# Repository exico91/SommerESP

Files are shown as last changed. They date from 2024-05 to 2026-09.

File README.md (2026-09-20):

# 🏠 SommerESP

A plug and play ESP32-C3 board to control Sommer garage doors based on ESPHOME

This combo is designed to replace the Sommer Conex Module and the Sommer Output OC Module. 

## ⚙️ How it works
The Sommer Conex Module is designed to replicate the press of the buttons on the controller of the garage door and the Sommer Output OC just provide the signal for the status and 24 Volts DC.  

This project takes the 24V and converts it to 3.3V for the ESP32-C3 module, the DC regulator on the power board can take from 4.5V to 40V and cleanly output 3.3V then transfer it to the Control board along with the status signal.  

The ESP controller simulate the press of the buttons using a pair of optocouplers, simple enough. You can also attach other things to this board, I left a couple of GPIOs on exposed pins along with the serial connection required to flash the module.

## 📋 Instructions
You can buy [here](https://www.tindie.com/products/exico91/sommeresp/) the kit that includes the two boards and a cable or you can build one yourself. You can find the BOM (bill of materials) [here](https://htmlpreview.github.io/?https://github.com/exico91/SommerESP/blob/main/Kicad/SommerESP/bom/ibom.html) and the gerber files [here](/Kicad/SommerESP/gerbers/). 
There are a lot of PCB Manufacturers. The most known are [PCBWay](https://www.pcbway.com/) and [JLCPCB](https://jlcpcb.com/). I used both and are good.

### 🔧 Installation
 1. Remove the plug from the wall, or cut off power to the Sommer garage door controller
 2. Write your firmware if you want or use it as is. You can find a basic yaml [here](/ESPHOME/esphome.yaml) or the ethernet module variant [here](/ESPHOME/esphome-eth.yaml). To do so you will need a serial programmer and set it to 3.3V, connect GND, VIN, RX and TX to the controller board and power it on while pressing BOOT on the board. When you are done remove the serial programmer. DO NOT connect the programmer while the board is connected to the power board or inserted in the Sommer controller.
 3. Open the controller but pay attention to the keypad cable when you remove the cover
 4. Place the board as shown, pay attention that both plugs are inserted:
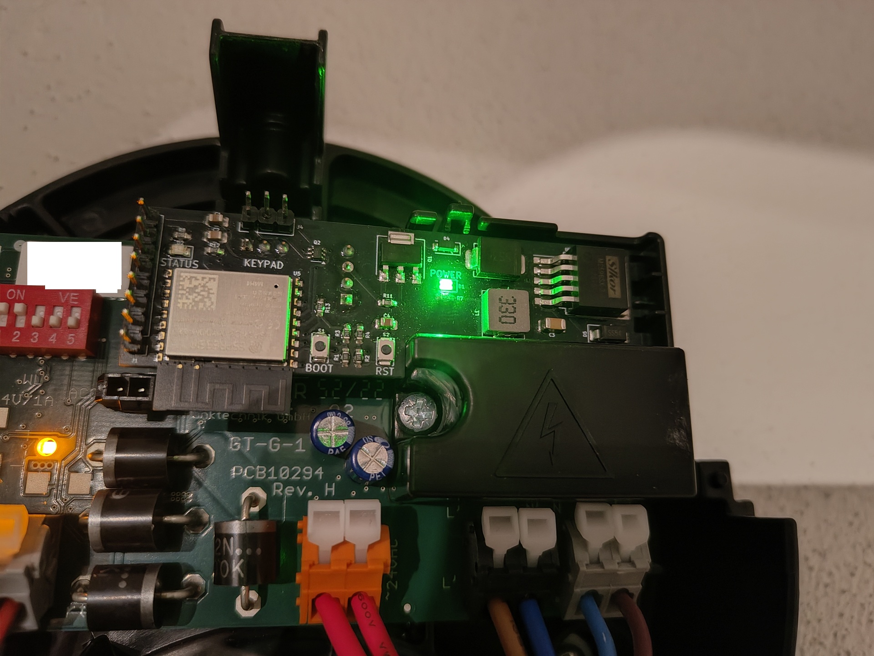
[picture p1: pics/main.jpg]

 5. Flip the first two switches to ON on the dip switch array on the Sommer controller
 6. Connect the keypad to the board in the same orientation as it was before (if present, some Sommers do not have a keypad)
 7. Close the cover and power it on. You should be able to see a wifi network and connect to it to configure the module.

> [!NOTE]
> The ethernet module (W5500) yaml is available [here](/ESPHOME/esphome-eth.yaml) and the KiCad project [here](/Kicad/SommerESP-ETHmodule/).

### 📡 External Antenna

If your installation requires better WiFi reception, an external antenna version is available. You will need:
 1. The SommerESP board in the version **without integrated antenna**, available on the [Tindie store](https://www.tindie.com/stores/exico91/)
 2. The **antenna kit** (includes antenna and U.FL adapter cable), also available on the [Tindie store](https://www.tindie.com/stores/exico91/)

Connect the adapter cable to the U.FL connector on the board and attach the external antenna.

### 🔌 Flashing and extra pins
To flash connect you serial programmer to the exposed pins on the controller board. DO NOT connect the programmer while the board is connected to the power board or inserted in the Sommer controller.
From top to bottom the pins are in this order:

3.3V
GPIO05
RX
TX
GPIO18
GPIO19
GPIO03
GND

Press BOOT while powering on the programmer to send the controller in flashing mode.

### 🔄 Factory reset
With the provided yaml, holding the BOOT button for 10 seconds and then releasing it factory resets the board (erases the saved Wi-Fi credentials and preferences, then reboots). It can also be triggered from Home Assistant with the "Factory Reset" button.

## ✅ Compatibility
This project should work with Sommer Base+, Pro+ and Evo+.
The main focus of this project is ESPHome and Homeassistant but you can flash whatever you want on the ESP32-C3.
Check [here](/pinout.md) for the pinout.

**Confirmed working models:**

| **Model**  | **Notes** | **Credits** |
|---|---|---|
| 9080 Base+ | The keypad plug is present but there is no keypad, just plug the SommerESP there. | tim-kiefer  |
| 2060 Evo+  | The keypad plug has 5 pins instead of 3. Just plug the module on the middle leaving pin 1 and 5 free. See photo for reference [here](/pics/2060+notes.jpg) | Severnt |
| 9110 Pro+  | Original installation that created this project. This model has a wall mount control board with a 2 button keypad. | Alessio D |
| S 9050 pro | Need to manually add the DIP switch selector. Check [here](https://github.com/exico91/SommerESP/issues/5#issuecomment-2755661908) | M3c4tr0x |
| A800 XL    | Compatible but the Conex pins are shifted. Requires board version 2 or jumper cables.                                                                    | [jkremlacek](https://github.com/jkremlacek) |

> [!WARNING]
> Please do check the distance between the power pins and the right pin on the button connector. This version of SommerESP is compatible with Sommer boards where the distance is around 9.5 mm or 7.5 mm, just check which is correct and solder the connector for the Conex section in the 9.5 (default) or 7.5 place. If you are buying from Tindie the default will be 9.5, if you need 7.5 please contact me.

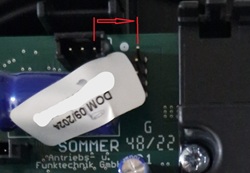
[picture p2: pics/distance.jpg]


## 📦 Release Log

### Firmware Release Log

| **Version** | **ESPHome** | **Changes** |
|---|---|---|
| 1.0 | — | Initial release |
| 1.3 | 2024.6.1 | Added compatibility for ESPHome 2024.6.1 |
| 2.0 | 2025.8.3 | Added compatibility for ESPHome 2025.8.3 |
| 3.0 | 2026.5.3 | Added compatibility for ESPHome 2026.5.3+, added Ethernet module version |
| 3.1 | 2026.5.3 | Cover stop function is now working |
| 3.2 | 2026.9.0 | Added factory reset function to the BOOT button (hold for 10 seconds) |

### Hardware Release Log

| **Version** | **Changes** |
|---|---|
| 1.0 - 2.0 | Dual board module with cable |
| 3.0 | Single board, adds Ethernet compatibility. Supports only 9.5 mm distance |
| 3.1 | Adds 7.5 mm distance compatibility |

## 💡 Origins
A thank you to https://github.com/jampez77/garage_door_sensor/ and https://github.com/azrael783/esphome_garagedoor_opener for giving me the ispiration to do this project, a lot of the code and core functionality is similar to these projects. Unfortunately neither did what I needed, cheap and invisible installation. Unfortunately the two Sommer modules (Conex and Output OC) are not cheap for what they are and using a DC-DC converter and relais externally is bulky and unsightly. I took the matter into my hands and now is almost plug and play and places where the two Sommer modules were.

A thank you to [M3c4tr0x](https://github.com/M3c4tr0x) for a part of the design of the new single board.

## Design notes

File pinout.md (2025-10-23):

### Pinout

The main chip is a ESP32-C3-WROOM-02

<table>
    <tbody>
        <tr>
            <td>
                PIN
            </td>
            <td>
                What is connected to
            </td>
        </tr>
        <tr>
            <td>
                GPIO2
            </td>
            <td>
                Strapping pin
            </td>
        </tr>
        <tr>
            <td>
                GPIO3
            </td>
            <td>
                GPIO Header 7th Pin
            </td>
        </tr>
        <tr>
            <td>
                GPIO4
            </td>
            <td>
                Analog signal from Sommer Controller
            </td>
        </tr>
        <tr>
            <td>
                GPIO5
            </td>
            <td>
                GPIO Header 2nd Pin
            </td>
        </tr>
        <tr>
            <td>
                GPIO6
            </td>
            <td>
                Open Button
            </td>
        </tr>
        <tr>
            <td>
                GPIO7
            </td>
            <td>
                Close Button
            </td>
        </tr>
        <tr>
            <td>
                GPIO8
            </td>
            <td>
                Strapping pin
            </td>
        </tr>
        <tr>
            <td>
                GPIO9
            </td>
            <td>
                BOOT button and strapping pin
            </td>
        </tr>
        <tr>
            <td>
                GPIO10
            </td>
            <td>
                Status Led
            </td>
        </tr>
                <tr>
            <td>
                GPIO18
            </td>
            <td>
                GPIO Header 5th pin
            </td>
        </tr>
                <tr>
            <td>
                GPIO19
            </td>
            <td>
                GPIO Header 6th pin
            </td>
        </tr>
        <tr>
            <td>
                GPIO20
            </td>
            <td>
                GPIO Header Serial RX 3rd pin
            </td>
        </tr>
        <tr>
            <td>
                GPIO21
            </td>
            <td>
                GPIO Header Serial TX 4th pin
            </td>
        </tr>
    </tbody>
</table>

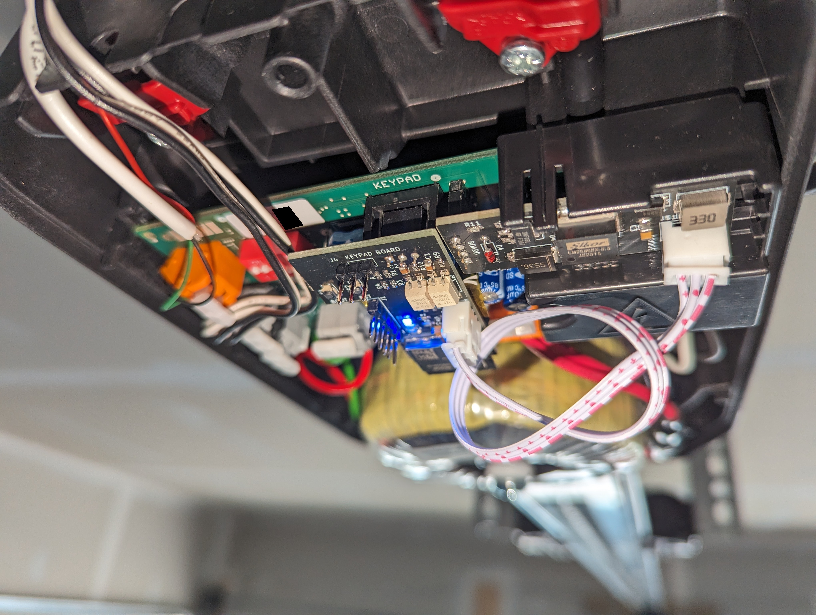
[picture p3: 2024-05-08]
pics/2060+notes.jpg

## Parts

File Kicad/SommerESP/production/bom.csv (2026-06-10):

Designator | Footprint | Quantity | Value | LCSC Part #
C1 | 0805 | 1 | 0805 10uf | C412252
C2 | 0805 | 1 | 0805 100nf | C412252
C3 | 1206 | 1 | 1206 220uf | C412252
C4 | 0805 | 1 | 0805 22uf | C412252
D1 | 0805 | 1 | LED Green | C397047
D2 | 0805 | 1 | LED Blue | C497961
D3 | SS32C | 1 | SS36 | C5449114
D4 | D_SOD-123 | 1 | 1N4148 | C402212
D5 | D_SMA | 1 | SS54 | C2902914
J1 | PinHeader_1x08_P2.54mm_Vertical | 1 | Serial programmer | C6332201
J3 | PinSocket_1x03_P2.54mm_Vertical | 1 | SOMMER CONEX BOARD | C146243
J4 | PinHeader_1x03_P2.54mm_Vertical | 1 | SOMMER CONEX KEYPAD | C49257
J6 | PinSocket_1x04_P2.54mm_Vertical | 1 | SOMMER OUTPUT OC | C2718488
L1 | L_Abracon_ASPI-0630LR | 1 | FAUL0630-330MT | C7461364
Q1 | STN3NF06L | 1 | STN3NF06 | C222218
Q2 | SOT-363_SC-70-6 | 1 | 2N7002DW | C5190214
R1, R2 | 0603 | 2 | 0603 100ohm | C3017758
R11, R7, R8 | 0603 | 3 | 0603 1k | C116692
R12, R13, R3, R4 | 0603 | 4 | 0603 10k | C2930027
S1, S2 | DEALON TD-1183SN-1.5H-160 | 2 | DEALON TD-1183SN | C2905192
U4 | TO-263-5_TabPin3 | 1 | LM2596SX-3.3/NOPB | C5186052
U5 | ESP32-C3-WROOM-02 | 1 | ESP32-C3-WROOM-02 | C2934560

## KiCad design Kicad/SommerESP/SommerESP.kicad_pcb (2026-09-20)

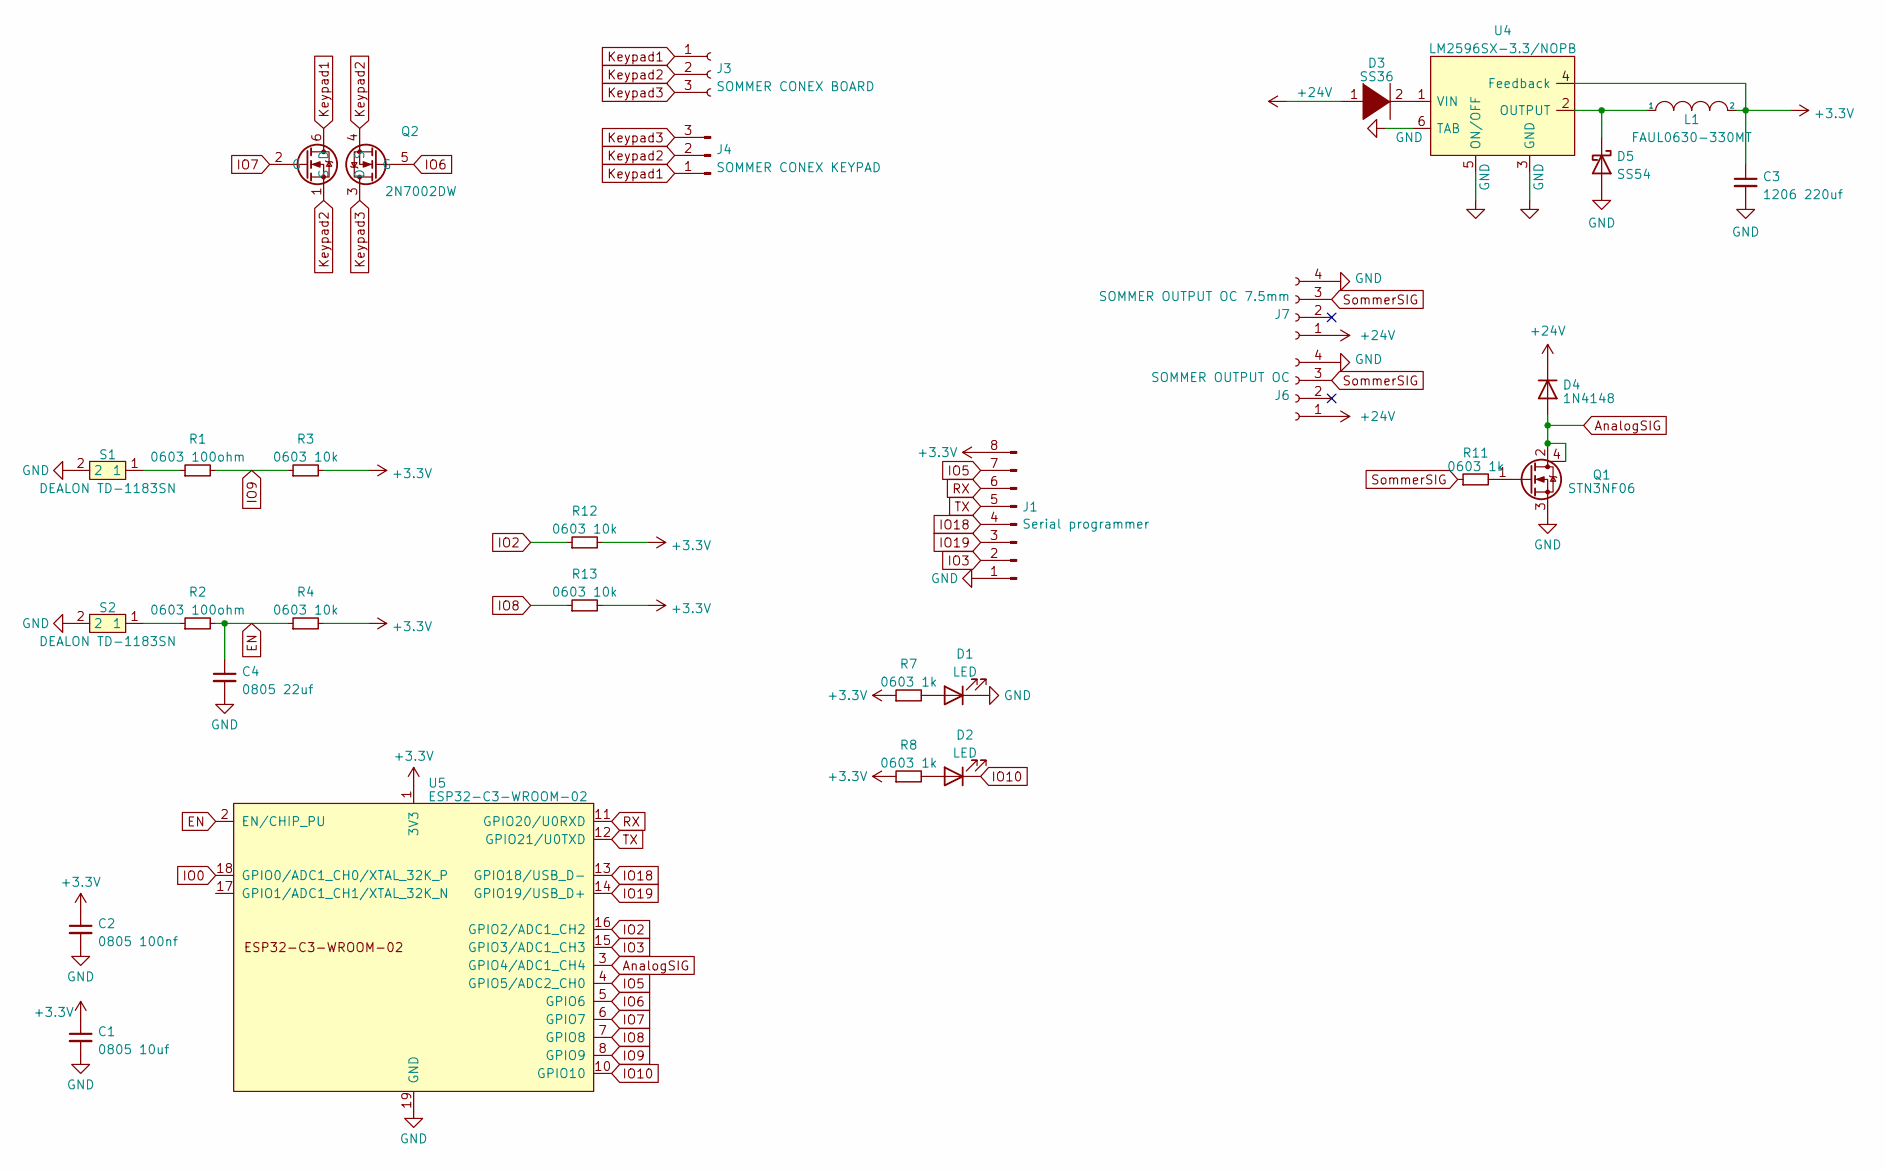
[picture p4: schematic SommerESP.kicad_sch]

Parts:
C1: 0805 10uf; C_0805_2012Metric_Pad1.18x1.45mm_HandSolder; LCSC PN C307525
C2: 0805 100nf; C_0805_2012Metric_Pad1.18x1.45mm_HandSolder; LCSC PN C5137467
C3: 1206 220uf; C_1206_3216Metric_Pad1.33x1.80mm_HandSolder; LCSC PN C412252
C4: 0805 22uf; C_0805_2012Metric_Pad1.18x1.45mm_HandSolder; LCSC PN C5674
D1: LED; LED_0805_2012Metric_Pad1.15x1.40mm_HandSolder; LCSC PN C397047
D2: LED; LED_0805_2012Metric_Pad1.15x1.40mm_HandSolder; LCSC PN C497961
D3: SS36; SS32C; LCSC PN C5449114
D4: 1N4148; D_SOD-123; LCSC PN C917030
D5: SS54; D_SMA; LCSC PN C2902914
J1: Serial programmer; PinHeader_1x08_P2.54mm_Vertical; LCSC PN C6332201
J3: SOMMER CONEX BOARD; PinSocket_1x03_P2.54mm_Vertical; LCSC PN C146243
J4: SOMMER CONEX KEYPAD; PinHeader_1x03_P2.54mm_Vertical; LCSC PN C49257
J6: SOMMER OUTPUT OC; PinSocket_1x04_P2.54mm_Vertical; LCSC PN C2718488
J7: SOMMER OUTPUT OC 7.5mm; PinSocket_1x04_P2.54mm_Vertical; LCSC PN C2718488
L1: FAUL0630-330MT; L_Abracon_ASPI-0630LR; LCSC PN C7461364
Q1: STN3NF06; STN3NF06L; LCSC PN C222218
Q2: 2N7002DW; SOT-363_SC-70-6; LCSC PN C5190214
R1, R2: 0603 100ohm; R_0603_1608Metric_Pad0.98x0.95mm_HandSolder; LCSC PN C3017758
R3, R4, R12, R13: 0603 10k; R_0603_1608Metric_Pad0.98x0.95mm_HandSolder; LCSC PN C2930027
R7, R8, R11: 0603 1k; R_0603_1608Metric_Pad0.98x0.95mm_HandSolder; LCSC PN C116692
S1, S2: DEALON TD-1183SN; DEALON TD-1183SN-1.5H-160; LCSC PN C2905192
U4: LM2596SX-3.3/NOPB; TO-263-5_TabPin3; LCSC PN C5186052
U5: ESP32-C3-WROOM-02; LCSC PN C2934560

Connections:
+3.3V: C1.1, C2.1, C3.1, J1.8, L1.2, R3.2, R4.2, R7.1, R8.1, R12.2, R13.2, U4.4 (Feedback), U5.1 (3V3)
+24V: D3.1 (K), D4.1 (K), J6.1, J7.1
AnalogSIG: D4.2 (A), Q1.2 (D), Q1.4 (D_TAB), U5.3 (GPIO4/ADC1_CH4)
EN: C4.1, R2.2, R4.1, U5.2 (EN/CHIP_PU)
GND: C1.2, C2.2, C3.2, C4.2, D1.1 (K), D5.2 (A), J1.1, J6.4, J7.4, Q1.3 (S), S1.2, S2.2, U4.3 (GND), U4.5 (ON/OFF), U4.6 (TAB), U5.9 (GND), U5.19 (GND)
IO0: U5.18 (GPIO0/ADC1_CH0/XTAL_32K_P)
IO2: R12.1, U5.16 (GPIO2/ADC1_CH2)
IO3: J1.2, U5.15 (GPIO3/ADC1_CH3)
IO5: J1.7, U5.4 (GPIO5/ADC2_CH0)
IO6: Q2.5 (G), U5.5 (GPIO6)
IO7: Q2.2 (G), U5.6 (GPIO7)
IO8: R13.1, U5.7 (GPIO8)
IO9: R1.2, R3.1, U5.8 (GPIO9)
IO10: D2.1 (K), U5.10 (GPIO10)
IO18: J1.4, U5.13 (GPIO18/USB_D-)
IO19: J1.3, U5.14 (GPIO19/USB_D+)
Keypad1: J3.1, J4.1, Q2.6 (D)
Keypad2: J3.2, J4.2, Q2.1 (S), Q2.4 (S)
Keypad3: J3.3, J4.3, Q2.3 (D)
unnamed: D1.2 (A), R7.2
unnamed: D2.2 (A), R8.2
unnamed: D3.2 (A), U4.1 (VIN)
unnamed: D5.1 (K), L1.1, U4.2 (OUTPUT)
unnamed: Q1.1 (G), R11.2
unnamed: R1.1, S1.1
unnamed: R2.1, S2.1
RX: J1.6, U5.11 (GPIO20/U0RXD)
SommerSIG: J6.3, J7.3, R11.1
TX: J1.5, U5.12 (GPIO21/U0TXD)

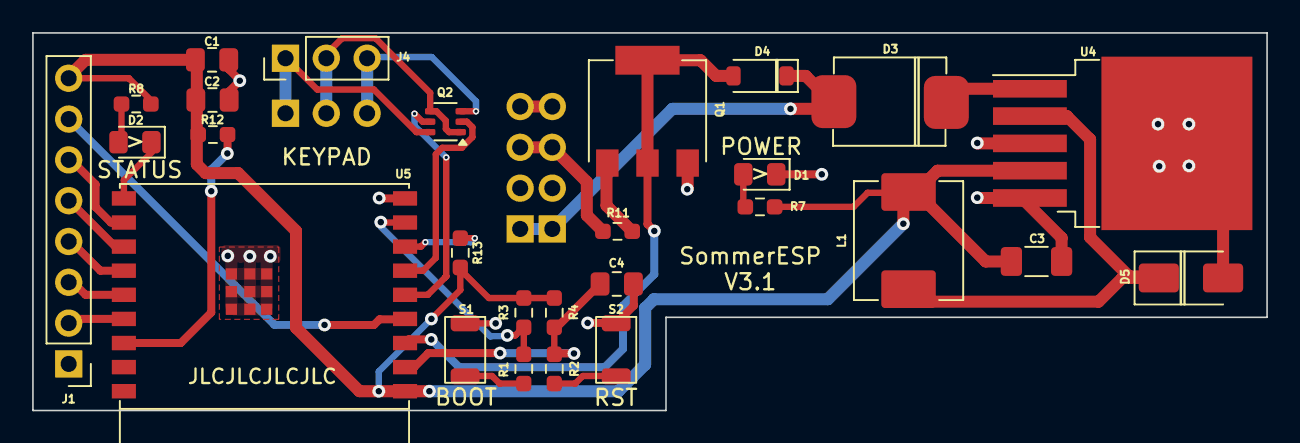
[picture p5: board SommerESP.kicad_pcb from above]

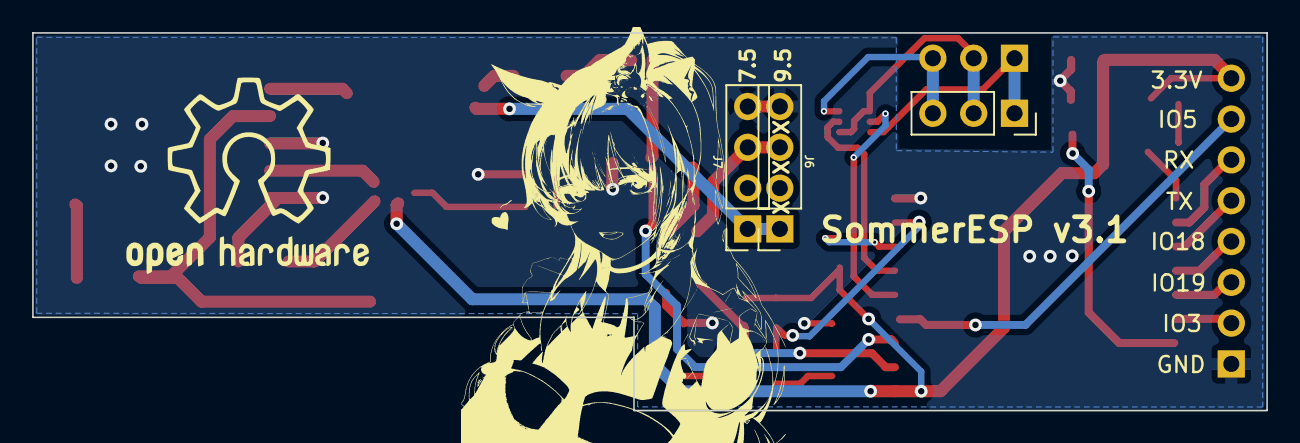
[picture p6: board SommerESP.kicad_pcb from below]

Board: 2 copper layers, 76.8 x 23.5 mm, 30 parts (3 on the bottom side), 28 nets.

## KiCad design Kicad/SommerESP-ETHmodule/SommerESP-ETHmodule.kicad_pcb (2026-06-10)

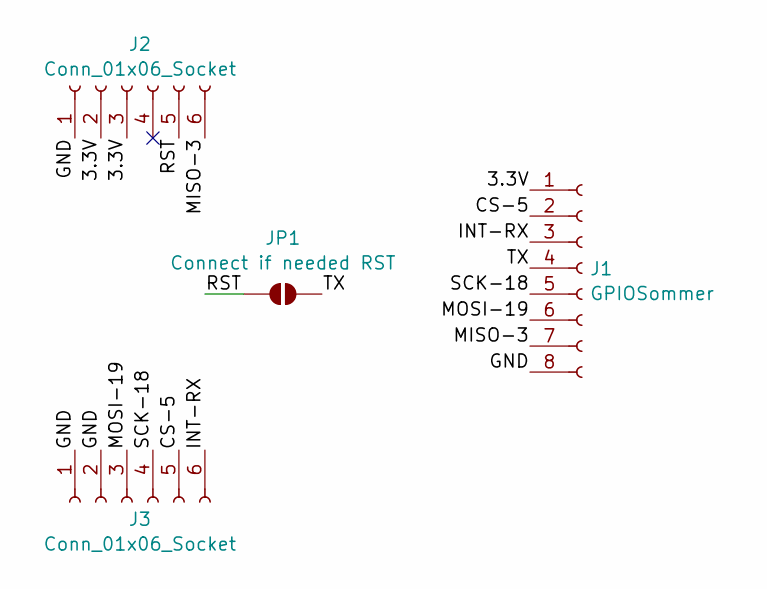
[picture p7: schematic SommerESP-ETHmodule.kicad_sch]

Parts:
J1: GPIOSommer; PinSocket_1x08_P2.54mm_Vertical
J2, J3: Conn_01x06_Socket; PinSocket_1x06_P2.54mm_Vertical
JP1: Connect if needed RST; SolderJumper-2_P1.3mm_Open_RoundedPad1.0x1.5mm

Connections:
/3.3V: J1.1, J2.2, J2.3
/CS-5: J1.2, J3.5
/GND: J1.8, J2.1, J3.1, J3.2
/INT-RX: J1.3, J3.6
/MISO-3: J1.7, J2.6
/MOSI-19: J1.6, J3.3
/RST: J2.5, JP1.1 (A)
/SCK-18: J1.5, J3.4
/TX: J1.4, JP1.2 (B)

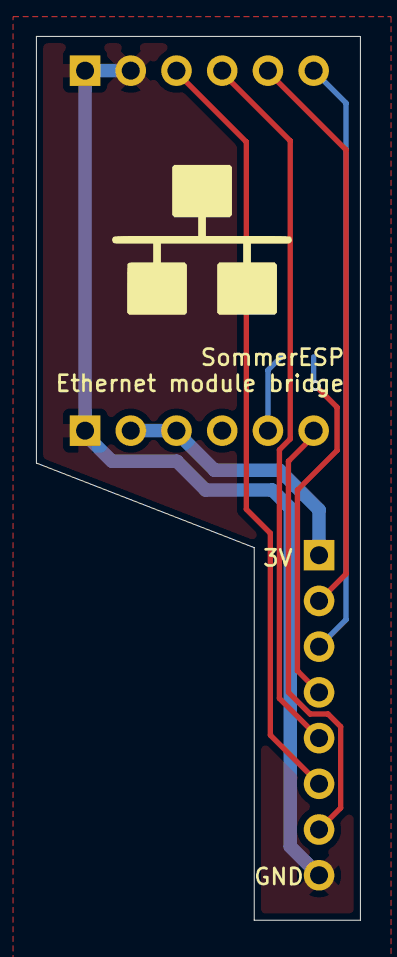
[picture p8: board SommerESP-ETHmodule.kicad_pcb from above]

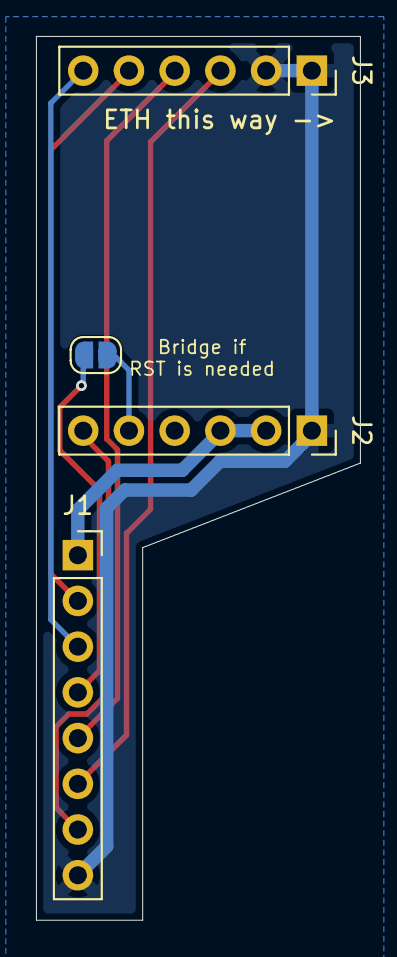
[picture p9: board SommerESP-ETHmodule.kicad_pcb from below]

Board: 2 copper layers, 18.0 x 49.1 mm, 4 parts (4 on the bottom side), 9 nets.

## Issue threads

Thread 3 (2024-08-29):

Works with S 9080 base+

tim-kiefer, 2024-08-29:
This is a pretty cool project! Thanks for all the work that went into it.

I can confirm that it also works with die base+ series. I just installed two and am happy with the result. Unlike the pro, the base has no wall-mounted unit. Instead, the two modules are installed in the ceiling-mounted unit. And there is no need to re-attach a keypad cable (because there is no keypad). Otherwise, it is just the same board.

Cheers
Tim

exico91, 2024-08-29:
Happy to know that! Perchance do you know your specific model? Ill just add it to the compatibility table

Closed 2024-08-29.

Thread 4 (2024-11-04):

Boot Loop - Firmware 1.3 - 2024.6.1

chrisblach, 2024-11-04:
I seem to be getting a boot loop on the SommerESP v1.1 control board. It has a ESP32-C3. I flashed it with the base image Firmware 1.3 - 2024.6.1.

Loops this message:
```
[11:33:47]ESP-ROM:esp32c3-api1-20210207
[11:33:47]Build:Feb  7 2021
[11:33:47]rst:0xf (BROWNOUT_RST),boot:0xd (SPI_FAST_FLASH_BOOT)
[11:33:47]SPIWP:0xee
[11:33:47]mode:DIO, clock div:1
[11:33:47]load:0x3fcd6100,len:0x438
[11:33:47]load:0x403ce000,len:0x918
[11:33:47]load:0x403d0000,len:0x24e4
[11:33:47]entry 0x403ce000
```

Is this to be expected without connecting to the Sommer board?

exico91, 2024-11-04:
Hello,

Yes, unfortunately with some serial adapters it boot loops at 3.3v because the adapter cannot supply enough current.
Its a hit or miss, I have two and one does this and the other not.
You can bypass the problem by supplying 5V to the power board and the serial connection to the control board instead of supplying directly the control board with the 3.3v on the header. Usually 5v comes "unfiltered" from the USB supply and it is enough current. The power board supports input voltages from 4.5V to 40V

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

chrisblach, 2024-11-15:
Thanks @exico91 , this was the exact problem! I changed the ping to the 5V on my programmer and was able to successfully flash the esp32. After flashing, the device was seen on my wifi and after plugging it into the Sommer unit it worked liked a charm!! Great project, I appreciate your efforts.

Do you think we can add some documentation about this or would this issue history be enough?

Closed 2024-11-16.

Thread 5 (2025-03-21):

[information] Sommer S 9050 pro works well with SommerESP

M3c4tr0x, 2025-03-21:
The project works well with a Sommer S 9050 motor.

However, it is necessary to add the DIP switch S1, which is not present on the board, and to set positions 1 and 2 to ON (or simply place wires on the first two positions of the DIP switch).
I have redesigned the board and made a smaller version since I had some components in stock.

exico91, 2025-03-21:
Hello, thank you for the feedback.
I have a smaller version in the works too :)

What do you mean that the dip switch is not present? they didnt place it on the board and its not populated?
Do you have some photos that I can add to the documentation?

M3c4tr0x, 2025-03-21:
Yes, that's exactly it. There's no dipswitch on the board, but the microcontroller handles the inputs well. Simply wire the dipswitch or jumper the pins to achieve the desired operation, as described in the README.md file.
DIP1 = ON: (button 1: open, button 2: close)
DIP2 = ON: (Output OC = door status)

I'll try to take some pictures of the assembly quickly.
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

M3c4tr0x, 2025-03-26:
Here are some photos of my creation based on this github

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

exico91, 2025-03-27:
Oh nice, it fits well? I think I will update my design too in the future, I have in the works a version that doesnt use optocouplers that is smaller but still two pieces but after that, if you are ok, I think that ill copy the design. Can you give me some measurements for the two sets of pins?

M3c4tr0x, 2025-03-27:
Yes, it's been working perfectly for several months now.
If necessary, I can send you the Kicad project directly; it might be easier.

exico91, 2025-03-27:
Maybe its a software bug, I will have to look into that.
Sure thing, send it over, Ill be sure to credit you when ill update the design.
info@gmservices.pro

M3c4tr0x, 2025-04-27:
Okay, I've emailed you the project. Sorry it took so long

exico91, 2025-04-29:
> Okay, I've emailed you the project. Sorry it took so long

No worries, received it.
Everyone is busy with life :)
Ive yet to take a look on it but thank you. Ill be sure to credit you in the new design.

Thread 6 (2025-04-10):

ESP doesn’t reconnect to Wi-Fi automatically after power loss

ButtersJuD, 2025-04-10:
Hi, thanks for your work on this great project!

I'm experiencing an issue with my SommerESP setup. After a power outage, the ESP module doesn't reconnect to my Wi-Fi network automatically. I always have to manually open the motor housing and press the Reset button on the ESP module to get it back online.

Is there something I might have missed in the configuration?
Should the module reconnect on its own after losing power?

Thanks in advance for any help or suggestions!

exico91, 2025-04-10:
No it should connect automatically.
Did you change the yaml in any way?

Also, we can try adding a static ip configuration to it and see if this fixes it

ButtersJuD, 2025-04-10:
Thanks for your reply!

I haven't been able to modify the YAML because I can't access the device through ESPHome. I'm still a bit new to all this, and ESPHome is asking me to connect the ESP module via USB in order to update or change the configuration.

Is there a way to make those changes over Wi-Fi, or do I need to physically connect it to my computer?

Thanks again for your help and patience!

ButtersJuD, 2025-04-10:
Thanks a lot for your help and guidance!

I managed to modify the YAML with the static IP, SSID, and password, and I successfully updated the ESP. I can now see it live in ESPHome — that’s already a big step forward!

Honestly, I was a bit hesitant to change the configuration before, afraid I might break something, so I really appreciate the clear instructions.

Unfortunately, the issue is still there: when I cut the power and turn the ESP back on, it doesn’t reconnect to the Wi-Fi automatically. I also don’t see its hotspot. The only way to get it back online is to press the reset button — after that, it connects right away.

So it seems the static IP didn’t fix the problem. Do you have any other idea of what might be causing this?

Thanks again for your help!

exico91, 2025-04-10:
https://esphome.io/components/wifi.html
You can try adding a fast_connect option or reboot_timeout to the wifi section.

I do not really know. It can be a design defect (this is my first public pcb after all)

exico91, 2025-04-10:
Also, from now on you can edit the configuration from homeassistant and install it using the wifi option when asked

severnt, 2025-04-12:
I've recently been having a similar issue as well after longer power outages. I've found that if I toggle the power to the opener quickly (i.e. unplug then plug back in), that also fixes it (as an alternative to opening it up and hitting RST).

In my case, I don't think the ESP32 wasn't getting far enough in the boot process to initialize wifi or even go into safe mode.

So, I'm thinking it might be a power up issue where the ESP32 is enabling before the power supply to it is stable, and in the case of a short power outage the power supply is stable enough to come to a good voltage faster. This didn't happen when I first installed everything, so maybe components in my opener are aging.

Espressif seems to recommend a delay using an RC circuit on EN:
- https://docs.espressif.com/projects/esp-hardware-design-guidelines/en/latest/esp32c3/schematic-checklist.html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
- https://dl.espressif.com/dl/schematics/esp32_devkitc_v4-sch.pdf

I'm planning on adding a 1 uF capacitor on mine to see if that helps (between the GND side of the RST button, and EN between R2-R4).

severnt, 2025-04-24:
Update in my case: Both LEDs were lit after power on and stayed on until I pressed RST. 1 uF capacitor didn't work, but a 22 uF capacitor seems to have fixed the issue.

exico91, 2025-04-25:
> Update in my case: Both LEDs were lit after power on and stayed on until I pressed RST. 1 uF capacitor didn't work, but a 22 uF capacitor seems to have fixed the issue.

Ok, I will add a 22uf, since you tested that works, in the new revision.

Also, I will need to fix the last two boards that I have, where did you put the cap? on the C3 pins or in parallel with the Resistor?

severnt, 2025-04-25:
I didn't take a photo unfortunately, but this is where I added it:

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

I used a through-hole electrolytic soldered to the GND side of S2, and R2 between R2/R4.

np, I'm pretty new too =)

exico91, 2025-05-05:
I added the Cap as you can see in the pictures to the boards that I will send tomorrow. So far so good for what I tested.

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

Again, thank you @severnt , I will implement the fix in the next version and credit you

Closed 2025-05-05.

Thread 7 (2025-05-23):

WIFI not shown

dartmann, 2025-05-23:
Hi,
after quite some time I finally got my garage door including a Sommer S9080 base+.

Now all is set up but unfortunately, the WiFi is not shown after I plugged in the Boards and cabled them. Of course, dip switches are set as you documented. See some pictures of the installation. After installation:
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

Power plugged in:
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

Am I doing something wrong respectively how can I troubleshoot?

Thank you for your support. Kind regards, David

exico91, 2025-05-24:
Hello, sorry to hear that. I usually check all of the boards before shipping.
The led lights are solid or one is blinking?

dartmann, 2025-05-24:
Yes, the blue one. The green stays as it is.

exico91, 2025-05-24:
Its a design bug unfortunately. It can happens with some installations.
You can check a permanent fix here: https://github.com/exico91/SommerESP/issues/6#issuecomment-2852250134
If you know someone that can solder a capacitor as shown in the image it should be permanently fixed. The cap value is 22uf and need to be installed with the correct polarity, GND to the button and the other leg on the resistor

dartmann, 2025-09-27:
Unfortunately, I was not able to do soldering so far. The hack to quickly turn off and on the power works for the few occasions when this situation appears again so far. Thank you anyway - a pity that my version does have this permanent fix already baked in.

Closed 2025-09-27.

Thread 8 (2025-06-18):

Wifi

DOliana, 2025-06-18:
Hi. I was wondering whether it would be possible to add an external antenna or at least an antenna connector. What do you think?

(contacting via tindie-store did not work for some reason...)

DOliana, 2025-06-21:
I think as long as there is an sma connector it should be good. I don't yet have your hardware, so I am not 100% sure if where it sits within the original housing and what the options to bring an antenna to the outside are.

I was thinking about an sma on board connector and then I would look for a second sma connector that can be fixed through a hole in the casing so that an antenna can be screwed on directly or (if needed) I could add a cable and put the antenna wherever local circumstances mandate it.

exico91, 2025-06-27:
@DOliana The antenna is quick to add, I just need to swap che ESP module with the one with a external antenna connector.
Adding ethernet on the other hand is... complicated.
While I agree that it would be nice to have people rarely have ethernet in the garage.
It can be a optional module, sure. I just need to check wich pins are needed

DOliana, 2025-06-27:
@exico91 you are right. Even though I think more people are getting ethernet as wallboxes become more common and ethernet is more reliable than wifi.
BTW: I am more on the software side of things so I cannot help much with hardware topics. If there is anything I can help with on the software let me know.

DOliana, 2025-07-23:
@exico91 were you able to find a suitable replacement ESP?

DOliana, 2025-07-23:
don't worry about ethernet if it's only for me - happy to try wifi first.
It's just that I have a wallbox right next to the Sommer controlunit that does use wifi and the connection is unstable (might be a bad antenna in the wallbox though).

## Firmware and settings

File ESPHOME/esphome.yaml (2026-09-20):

esphome:
  name: sommeresp
  name_add_mac_suffix: true
  project:
    name: "esphome.sommeresp"
    version: "3.0"

substitutions:
  device_name: "SommerESP"
  hotspot_password: "sommeresp"
  webserver_password: "sommeresp"

  project_name: "SommerESP by exico91"
  project_version: "3.0"


esp32:
  board: esp32-c3-devkitm-1
  framework:
    type: arduino


# Enable logging
logger:

# Enable Home Assistant API
api:

ota:
  - platform: esphome

wifi:
# Uncomment these two lines to enable autoconnect
#  ssid: ${wifi_ssid}
#  password: ${wifi_password}

  # Enable fallback hotspot (captive portal) in case wifi connection fails
  ap:
# Uncomment this line to set a custom SSID instead of default name+mac
#    ssid: "SSID"

# Uncomment to setup a password for the hotspot
#    password: ${hotspot_password}
  
  # Optional manual IP
#  manual_ip:
#    static_ip: 192.168.82.208
#    gateway: 192.168.82.1
#    subnet: 255.255.255.0


captive_portal:
    
# Enable Web server (optional).
web_server:
  port: 80

# Uncomment to setup user and password for the dashboard
#  auth:
#    username: "admin"
#    password: ${webserver_password}

#enable bluetooth proxy
#bluetooth_proxy:

text_sensor:
  # Expose ESPHome version as sensor.
  - platform: version
    name: ${device_name} ESPHome Version
  # Expose WiFi information as sensors.
  - platform: wifi_info
    ip_address:
      name: ${device_name} IP
    ssid:
      name: ${device_name} SSID
    
sensor:
  - platform: wifi_signal
    name: ${device_name} Wifi Signal Strength
    update_interval: 60s
  - platform: uptime
    name: ${device_name} Uptime
  - platform: adc
    pin: 4
    name: "Door Feedback"
    update_interval: 2s
    id: status_feedback
    internal: True

binary_sensor:
  - platform: analog_threshold
    name: "Door status"
    sensor_id: status_feedback
    threshold: 0.015
    device_class: garage_door
    id: door_status
    filters:
      - invert:
    internal: True

  # BOOT button: hold for 10s to factory reset. It acts on release, so the
  # reboot never happens with GPIO9 held low (which would enter download mode).
  - platform: gpio
    pin:
      number: GPIO9
      mode: INPUT_PULLUP
      inverted: true
    id: boot_button
    internal: true
    on_click:
      min_length: 10s
      max_length: 60s
      then:
        - button.press: factory_reset_button

globals:
  - id: last_direction
    type: int
    restore_value: no
    initial_value: '0'  # 0=idle, 1=opening, 2=closing

switch:
  - platform: gpio
    pin: 
      number: 7
      #inverted: True
    name: "Garage door Open Switch"
    id: open_switch
    on_turn_on:
      - delay: 250ms
      - switch.turn_off: open_switch
    restore_mode: ALWAYS_OFF
  - platform: gpio
    pin: 
      number: 6
      #inverted: True
    name: "Garage door close Switch"
    id: close_switch
    on_turn_on:
      - delay: 250ms
      - switch.turn_off: close_switch
    restore_mode: ALWAYS_OFF
  - platform: restart
    name: "Restart ESP"

button:
  - platform: factory_reset
    name: "Factory Reset"
    id: factory_reset_button
    entity_category: diagnostic

cover:
  - platform: template
    device_class: garage
    name: "Garage door"
    open_action:
      - globals.set:
          id: last_direction
          value: '1'
      - switch.turn_off: close_switch
      - switch.turn_on: open_switch
      - delay: 250ms
      - switch.turn_off: open_switch
    close_action:
      - globals.set:
          id: last_direction
          value: '2'
      - switch.turn_off: open_switch
      - switch.turn_on: close_switch
      - delay: 250ms
      - switch.turn_off: close_switch
    stop_action:
      - if:
          condition:
            lambda: 'return id(last_direction) == 1;'
          then:
            - switch.turn_on: open_switch
            - delay: 250ms
            - switch.turn_off: open_switch
          else:
            - if:
                condition:
                  lambda: 'return id(last_direction) == 2;'
                then:
                  - switch.turn_on: close_switch
                  - delay: 250ms
                  - switch.turn_off: close_switch
      - globals.set:
          id: last_direction
          value: '0'
    #optimistic: true
    lambda: |-
      if (id(door_status).state) {
        return COVER_OPEN;
      } else {
        return COVER_CLOSED;
      }
    #assumed_state: true

status_led:
  pin:
    number: 10
    inverted: true
    

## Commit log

2023-10-09 First upload
    [SommerESP-B_Cu.gbr, SommerESP-B_Mask.gbr, SommerESP-B_Paste.gbr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]
2023-10-09 Added instructions
    [SommerESP-B_Cu.gbr, SommerESP-B_Mask.gbr, SommerESP-B_Paste.gbr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]
2023-10-21 Updated description and yaml
    [SommerESP.kicad_pcb]
2023-10-26 removed backups
    inverted up and down pins after testing
    [esphome.yaml]
2023-12-04 Update esphome.yaml
    Added some options and better device naming
2024-01-13 Found an error in the schematic for Diode D4. Was inverted in the schematic but correct in the PCB and Photos.
    Thank you to Stefano Gnocato for pointing that out!
    [SommerESP.kicad_pcb, SommerESP.kicad_sch]
2024-01-25 Updated the check for door status from analog threshold to gpio with a pullup. This should be less prone to error and free some computational power
    Thanks to Stefano Gnocato for the input!
    [esphome.yaml]
2024-05-08 Updated Kicad to version 8 Added references to LCSC part numbers in the project and BOM Cleaned up a bit of silkscreen text and added some references Added JLCJLCJLCJLC on the silkscreen for the orde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
    [BOM-SommerESP.csv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]
2025-09-06 Updated to V2. This is a transition version.
    Updated yaml and added M3c4tr0x confirmation of
    board working
    [SommerESP-B_Cu.gbr, SommerESP-B_Mask.gbr, SommerESP-B_Paste.gbr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]
2025-10-23 Version 3.0 of SommerESP
    [BOM-SommerESP.csv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]
2026-06-10 - Add W5500 ethernet ESPHome config (esphome-eth.yaml) - Split KiCad project into SommerESP/ and SommerESP-ETHmodule/ - Update README: emojis, ethernet yaml link, external antenna instructions
    [SommerESP-B_Cu.gbr, SommerESP-B_Mask.gbr, SommerESP-B_Paste.gbr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]
2026-06-10 Update README with A800 XL compatibility details
    Added compatibility note for A800 XL model regarding Conex pin shift and board version requirements.
